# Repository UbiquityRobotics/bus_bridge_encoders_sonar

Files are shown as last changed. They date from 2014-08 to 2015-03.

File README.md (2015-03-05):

# bus_bridge_encoders_sonar

The are currently 4 revisions -- `rev_a`, `rev_b`, `rev_c`,
and `rev_d`.  The schematic is available as bus_bridge_encoders_sonar.pdf`
or as `bus_bridge_encoders_sonar.svg` in the appropriate revision
directory.

## Rev. A Issues

* Tie off unused inputs of U7 to 0V or 5V. [x]

* Replace R8, R9, R10, R11, R12, R13 with a 10K ohm SIP package. [x]

* Add protection diodes to the motor outputs.  The 754410 does
  **not** have protection diodes like the L793D did.  [No.  If
  it is an issue, use the L293D instead.]

* Adding a 2x3 pin ISP programming header. [x]

* The U8 TXD (pin 1) and RXD (pin 4) are swapped. [x]

* Replace the R17, R18, R20, R21 voltage dividers with 100K pull-ups. [x]

* Add a 100K pull up U7A pin 1 to protect against U8 not
  being plugged in. [x]

* Combine Encoder and Motor onto a single 2x4 ribbon cable. [x]

* Add an LED that can be blinked. [x]

## Rev. B Issues

* Connected U8 STBY (pin 8) to a processor pin [x]

## Rev. C Docummentation

<Table Border="1">
    <TR>
    </TR><TR>
	<TH>Arduino Name</TH>
	<TH>AVR Port</TH>
	<TH>Function</TH>
    </TR><TR>
	<TD>D0</TD>
	<TD>PD0/RXD</TD>
	<TD>USART Receive</TD>
    </TR><TR>
	<TD>D1</TD>
	<TD>PD0/TXD</TD>
	<TD>USART Transmit</TD.
    </TR><TR>
	<TD>D2</TD>
	<TD>PD3</TD>
	<TD>SONAR0_TRIG</TD>
    </TR><TR>
	<TD>D3</TD>
	<TD>PD3/OC2B</TD>
	<TD>SONAR0_ECHO</TD>
    </TR><TR>
	<TD>D4</TD>
	<TD>PD4</TD>
	<TD>SONAR1_TRIG</TD>
    </TR><TR>
	<TD>D5</TD>
	<TD>PD6/OC0B</TD>
	<TD>SONAR1_ECHO</TD>
    </TR><TR>
	<TD>D6</TD>
	<TD>PD6/OC0A</TD>
	<TD>ENC_EN</TD>
    </TR><TR>cc
	<TD>D7</TD>
        <TD>PD7<TD>
	<TD>1A</TD>
    </TR><TR>
	<TD>D8</TD>
	<TD>PB0<TD>
	<TD>4A</TD>
    </TR><TR>
	<TD>D9</TD>
	<TD>PB1/OC1A</TD>
	<TD>EN34</TD>
    </TR><TR>
	<TD>D10</TD>
	<TD>PB2/OC1B</TD>
	<TD>EN12</TD>
    </TR><TR>
	<TD>D11</TD>
	<TD>PB3/OC2A</TD>
	<TD>3A</TD>
    </TR><TR>
	<TD>D12</TD>m
	<TD>PB4</TD>
	<TD>2A</TD>
    </TR><TR>
	<TD>D13</TD>
	<TD>PB5</TD>
	<TD>LED</TD>
    </TR><TR>
	<TD>A0</TD>
	<TD>PC0</TD>
	<TD>ENC1_A</TD>
    </TR><TR>
	<TD>A1</TD>
	<TD>PC1</TD>
	<TD>ENC1_B</TD>
    </TR><TR>
	<TD>A2</TD>
	<TD>PC2</TD>
	<TD>ENC2_A</TD>
    </TR><TR>
	<TD>A3</TD>
	<TD>PC3</TD>
	<TD>ENC2_B</TD>
    </TR><TR>
	<TD>A4</TD>
	<TD>PC4</TD>
	<TD>CAN_STBY</TD>
    </TR><TR>
	<TD>A5</TD>
	<TD>PC5</TD>
	<TD>-</TD>
    </TR>
</Table>

## Rev. C Issues

* Schematic should label C13 as 1uF. [x]

* Schematic should label R4 as 120_1%. [x]

* Schematic has BGND and BPWR swapped on root diagram. [x]

* Make sure regulator input capacitors can take 30V.  Probably switch
  over to aluminum electrolytic capacitor. [x]

* Move ISP connector up to make more room for Atmel-ICE connector. [x]

* Between Dual Slot Encoder (Rev. D) and Rev. C of this
  board, pins 4 and 5 are swapped as are pins 6 and 7.
  [change dual slot encoders instead]
  See below:

<BlockQuote>
<Pre>
     BBES-C       DSE-D
    ===========================
     MOTOR_A   1  MOTOR_A
     MOTOR_A   2  MOTOR_A
     LOG_5V    3  LPWR (=5V)
     LGND      4  QUAD_A
     QUAD_A    5  LGND (not really used)
     QUAD_B    6  LED_EN
     LED_EN    7  QUAD_B
     LED_5V    8  BPWR
     MOTOR_B   9  MOTOR_B
     MOTOR_B  10  MOTOR_B
</Pre>
</BlockQuote>

## Rev. D Issues

* The vertical resistors are hard to solder.  Think about switching

* Update schematic to specifiy electrolytic capacistors for input
  voltage regulators.

* The C5 is too close to the mounting hole.

* Think about adding an LED jumper block.

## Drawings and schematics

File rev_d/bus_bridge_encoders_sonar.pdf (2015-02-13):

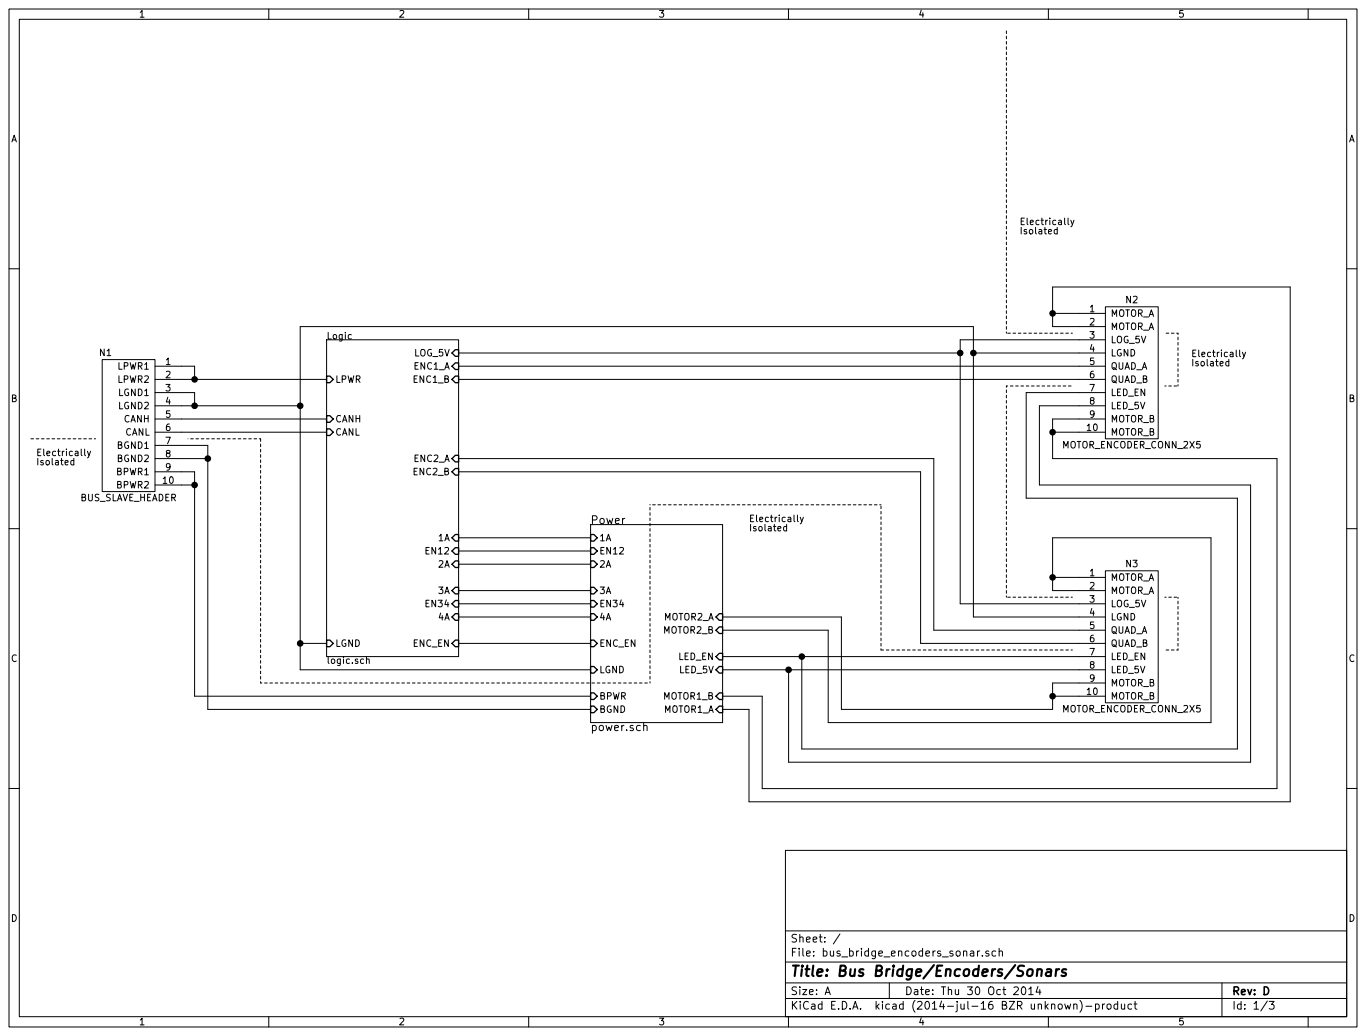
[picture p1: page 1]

File: bus_bridge_encoders_sonar.sch Sheet: /
Id: 1/3 Title: Bus Bridge/Encoders/Sonars

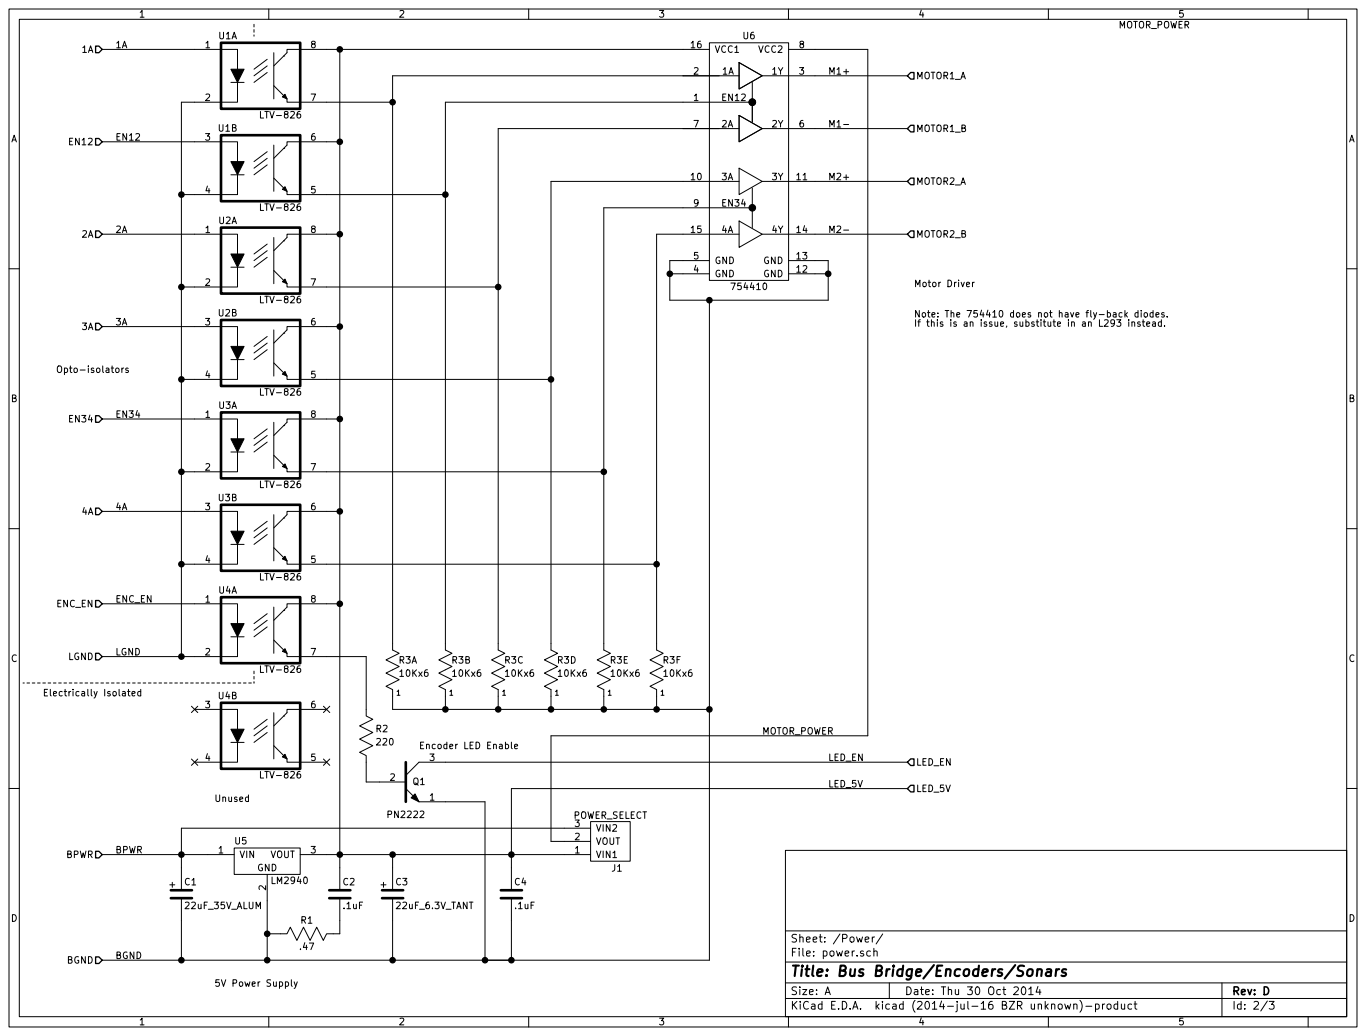
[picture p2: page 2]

If this is an issue, substitute in an L293 instead. LED_5V MOTOR_POWER

File: power.sch Sheet: /Power/ BPWR

Id: 2/3 Title: Bus Bridge/Encoders/Sonars

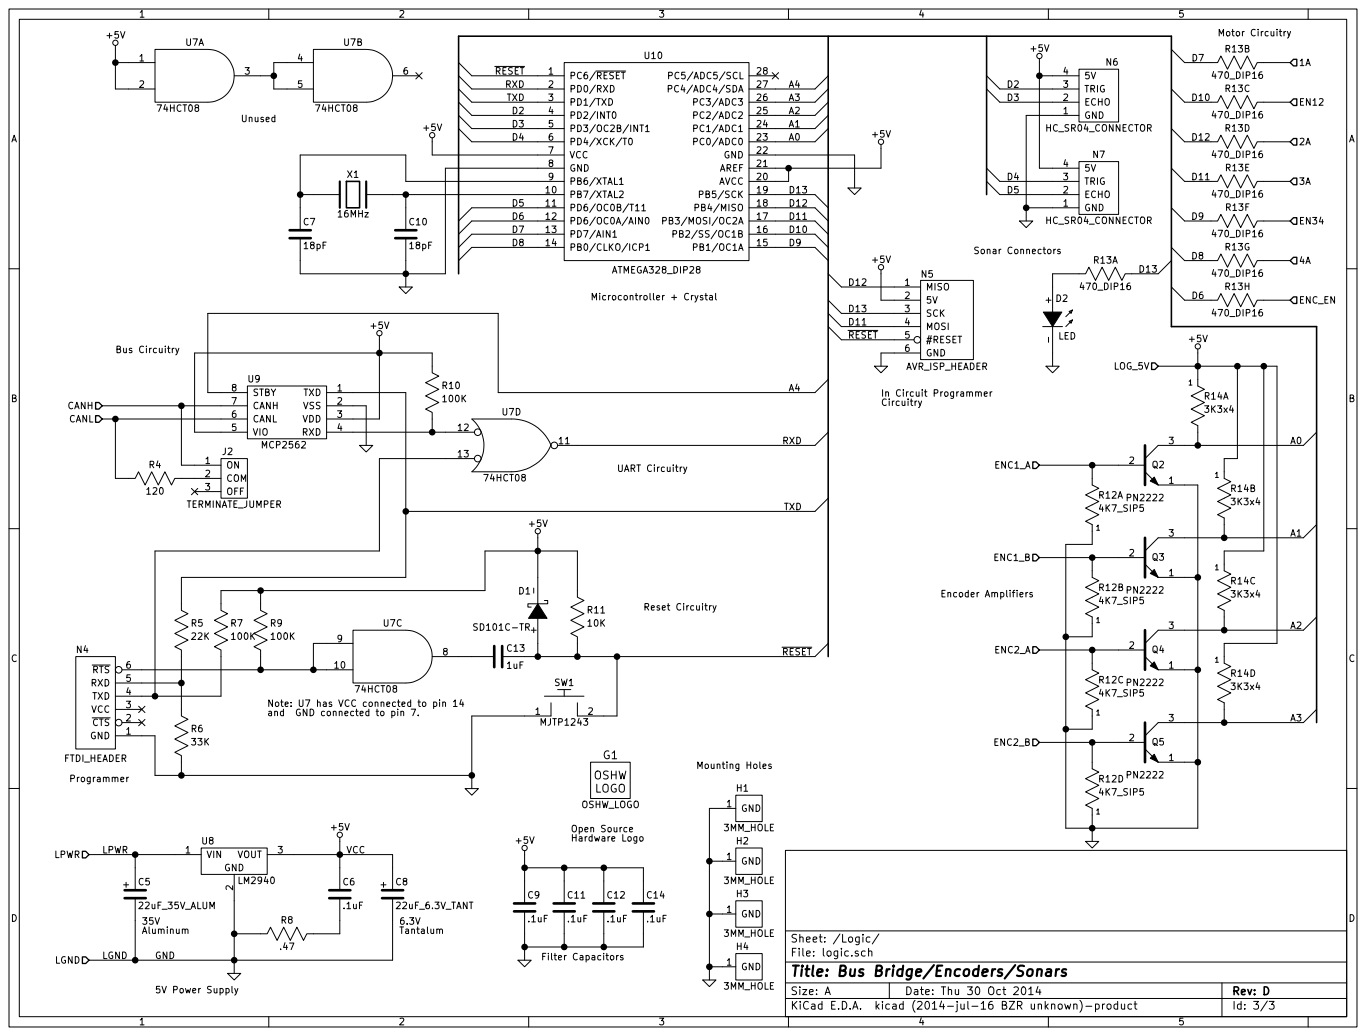
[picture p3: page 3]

UnusedNote: U7 has VCC connected to pin 14

and GND connected to pin 7.

File: logic.sch
Id: 3/3 Title: Bus Bridge/Encoders/Sonars

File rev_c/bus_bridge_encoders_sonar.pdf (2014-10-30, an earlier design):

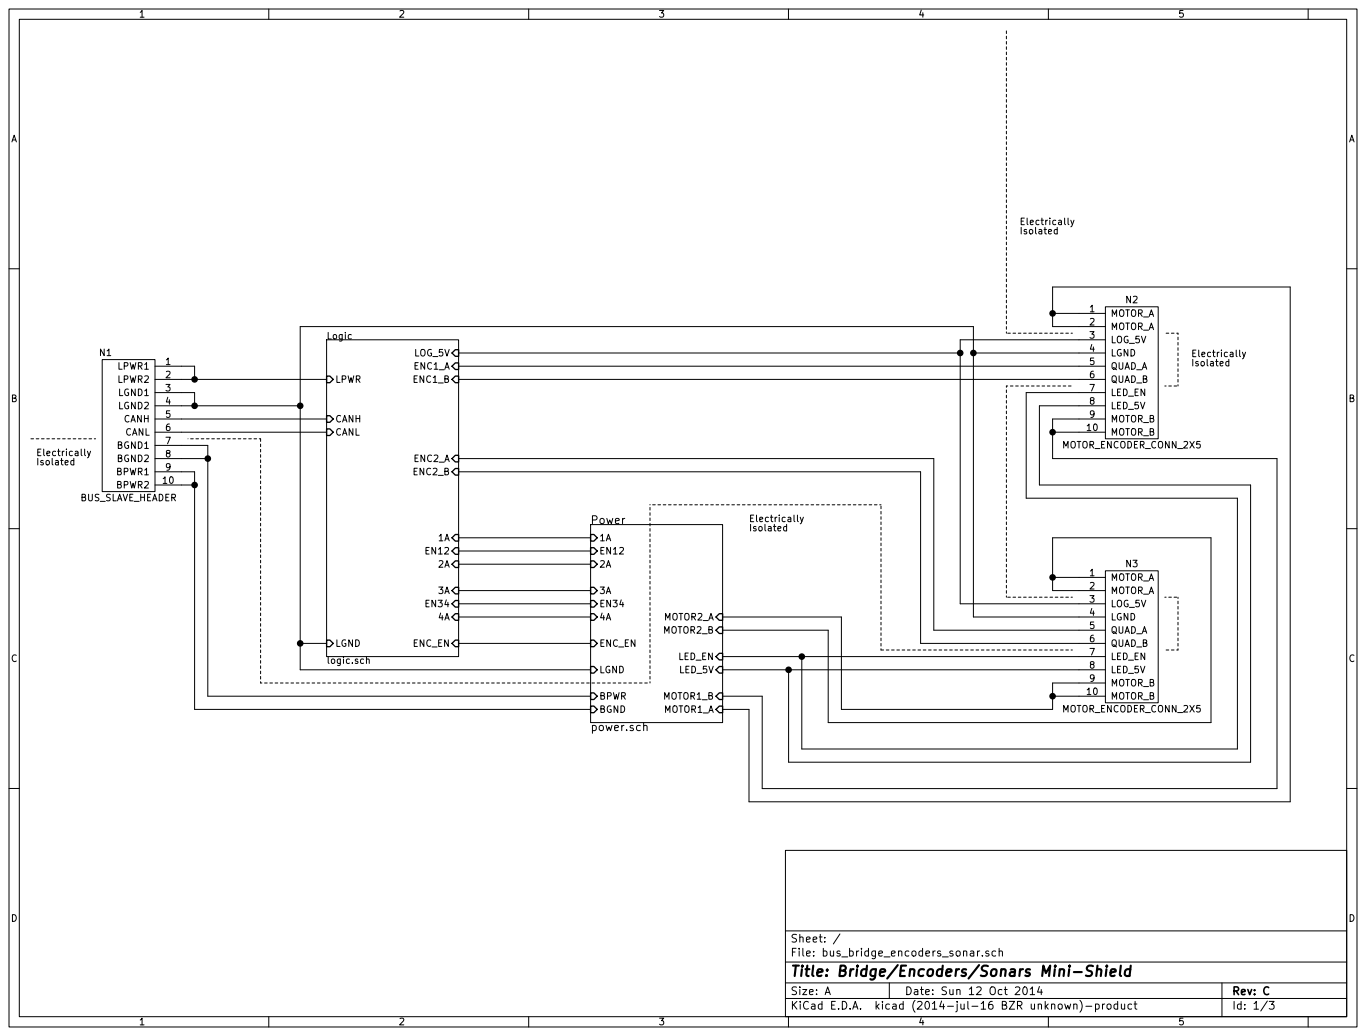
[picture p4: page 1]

File: bus_bridge_encoders_sonar.sch Sheet: /
Id: 1/3 Title: Bridge/Encoders/Sonars Mini-Shield

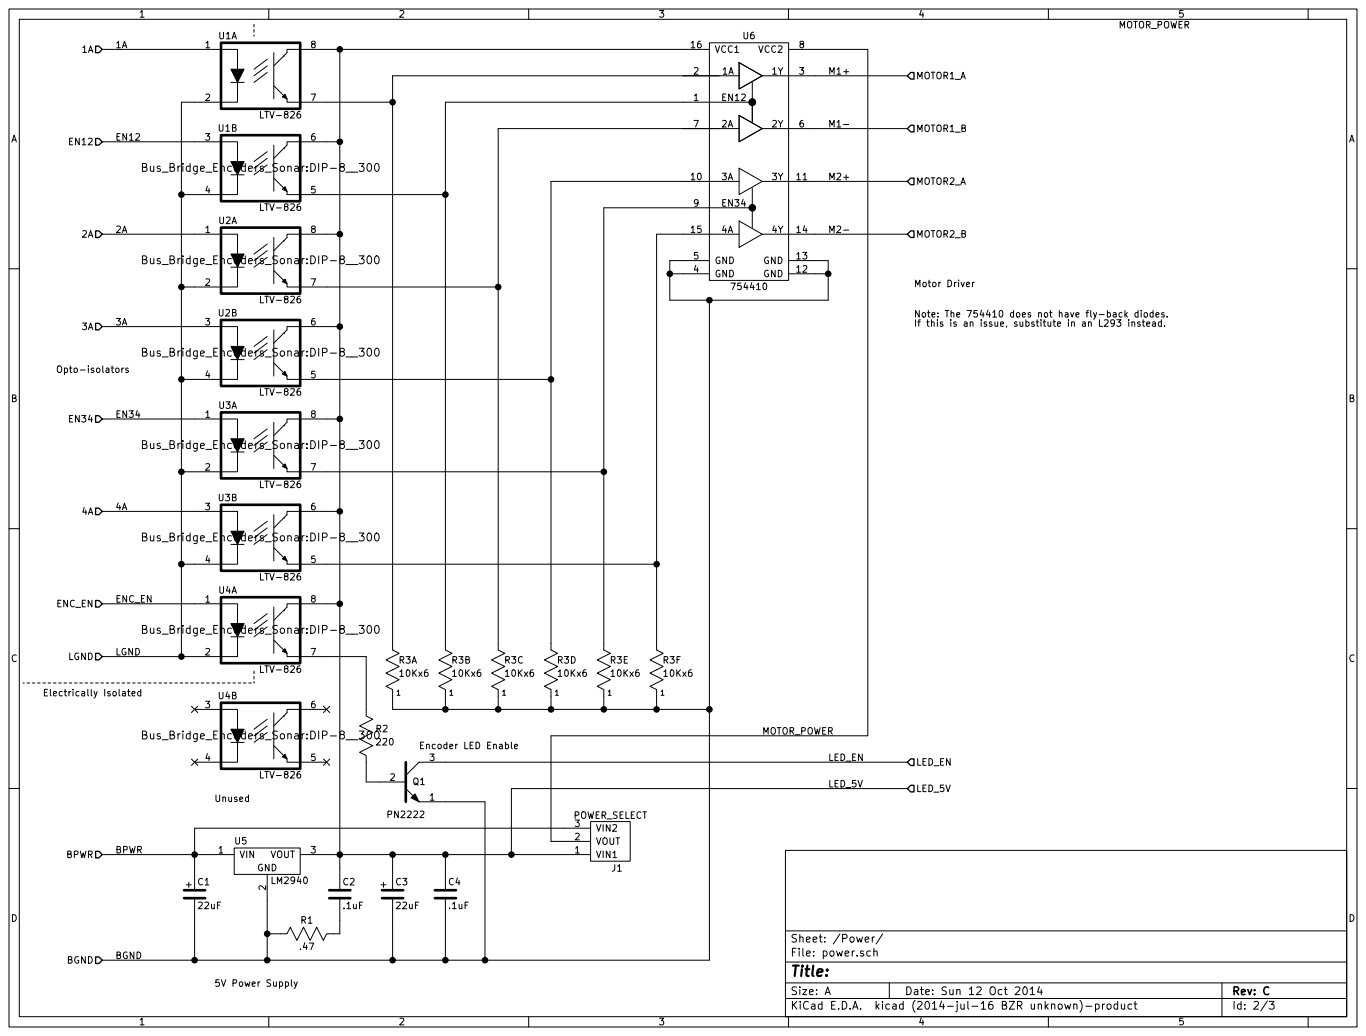
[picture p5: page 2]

If this is an issue, substitute in an L293 instead. LED_5V MOTOR_POWER

File: power.sch Sheet: /Power/ BPWR

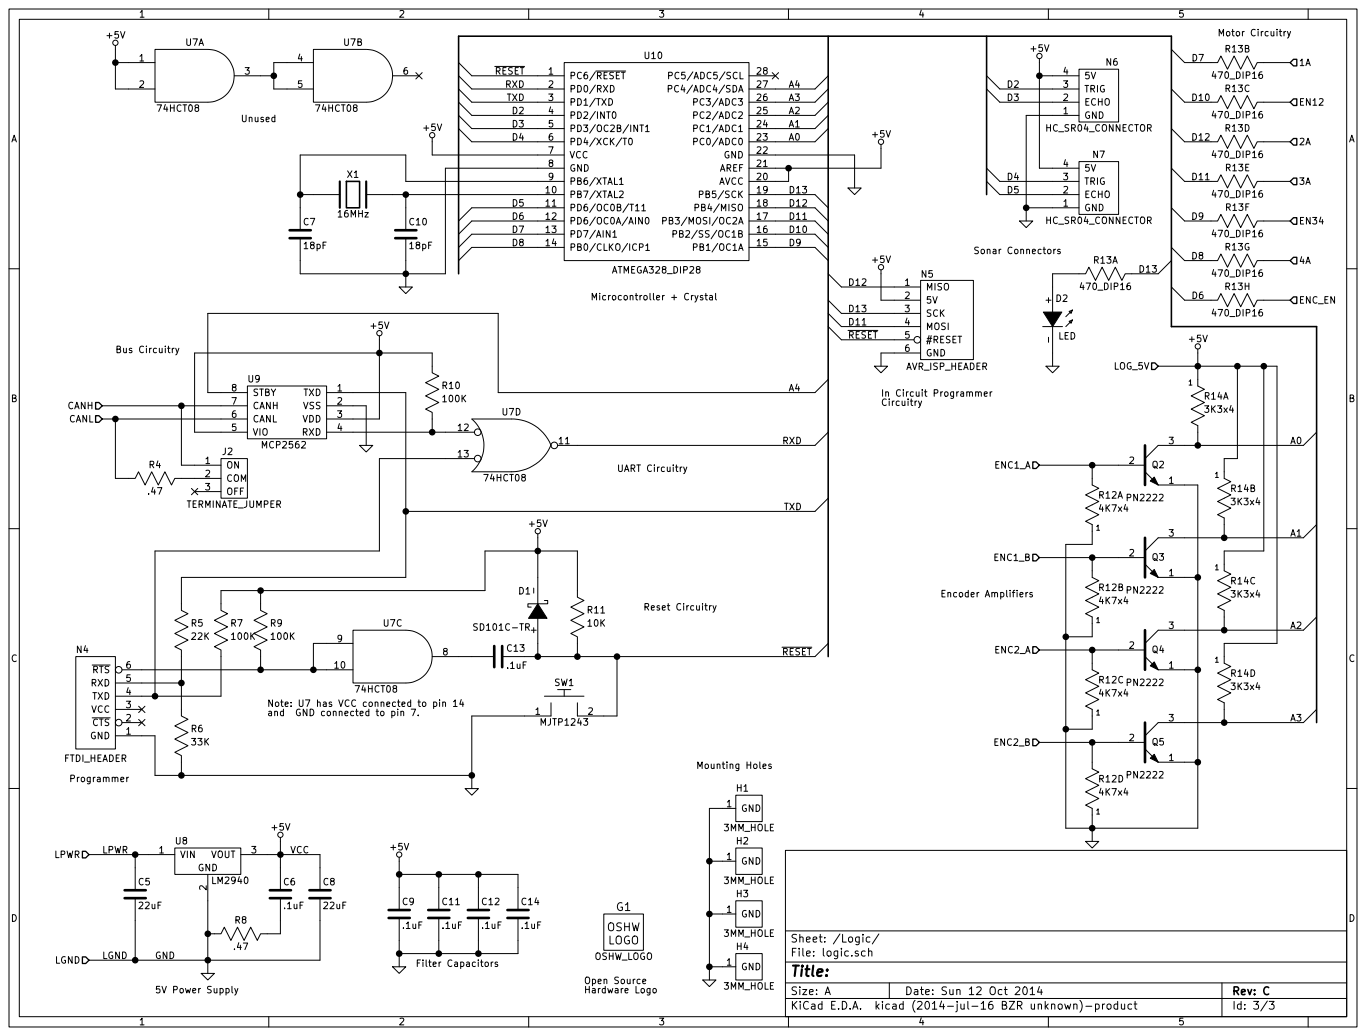
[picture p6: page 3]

UnusedNote: U7 has VCC connected to pin 14

and GND connected to pin 7.

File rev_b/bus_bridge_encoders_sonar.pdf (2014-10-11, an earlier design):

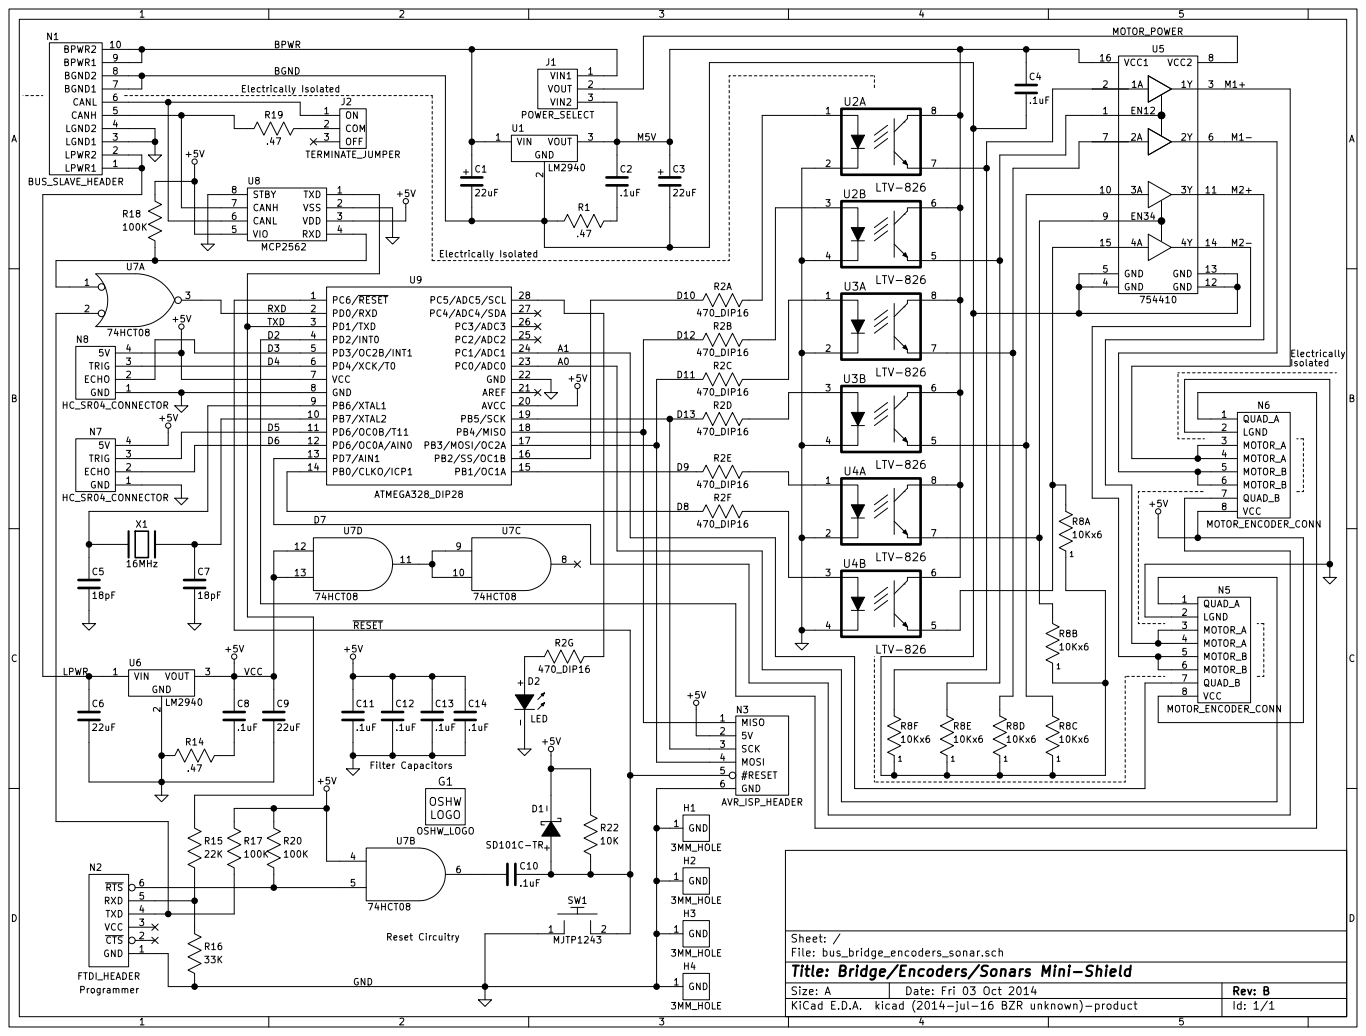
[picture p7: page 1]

File: bus_bridge_encoders_sonar.sch Sheet: / GND 1 H1

Id: 1/1 Title: Bridge/Encoders/Sonars Mini-Shield

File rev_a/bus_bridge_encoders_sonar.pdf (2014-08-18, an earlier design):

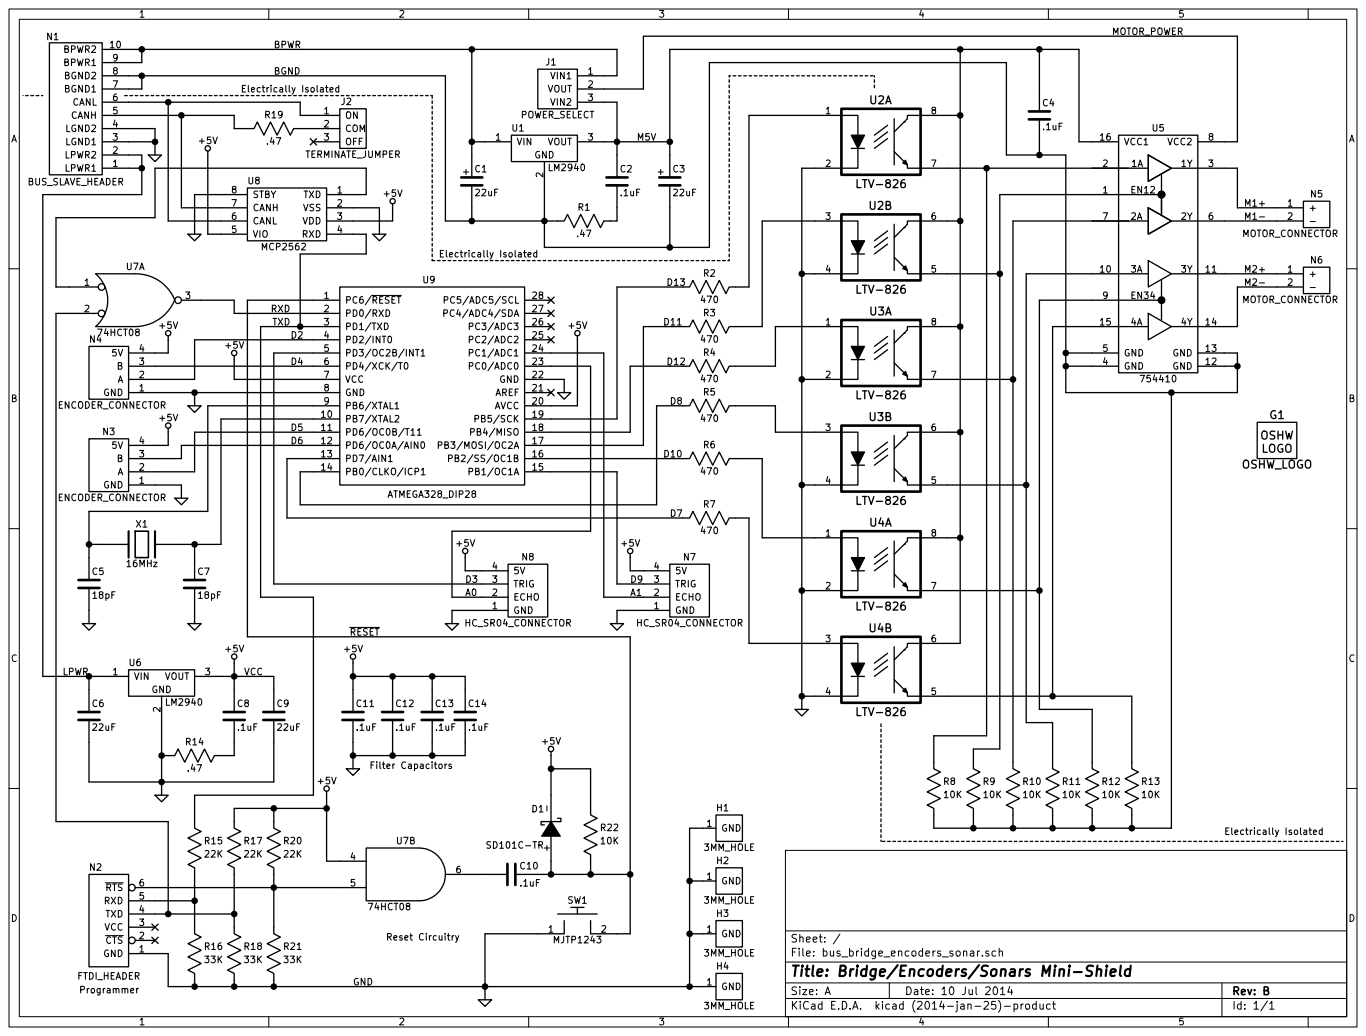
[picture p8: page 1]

File: bus_bridge_encoders_sonar.sch Sheet: / GND 1 H1

Id: 1/1 Title: Bridge/Encoders/Sonars Mini-Shield

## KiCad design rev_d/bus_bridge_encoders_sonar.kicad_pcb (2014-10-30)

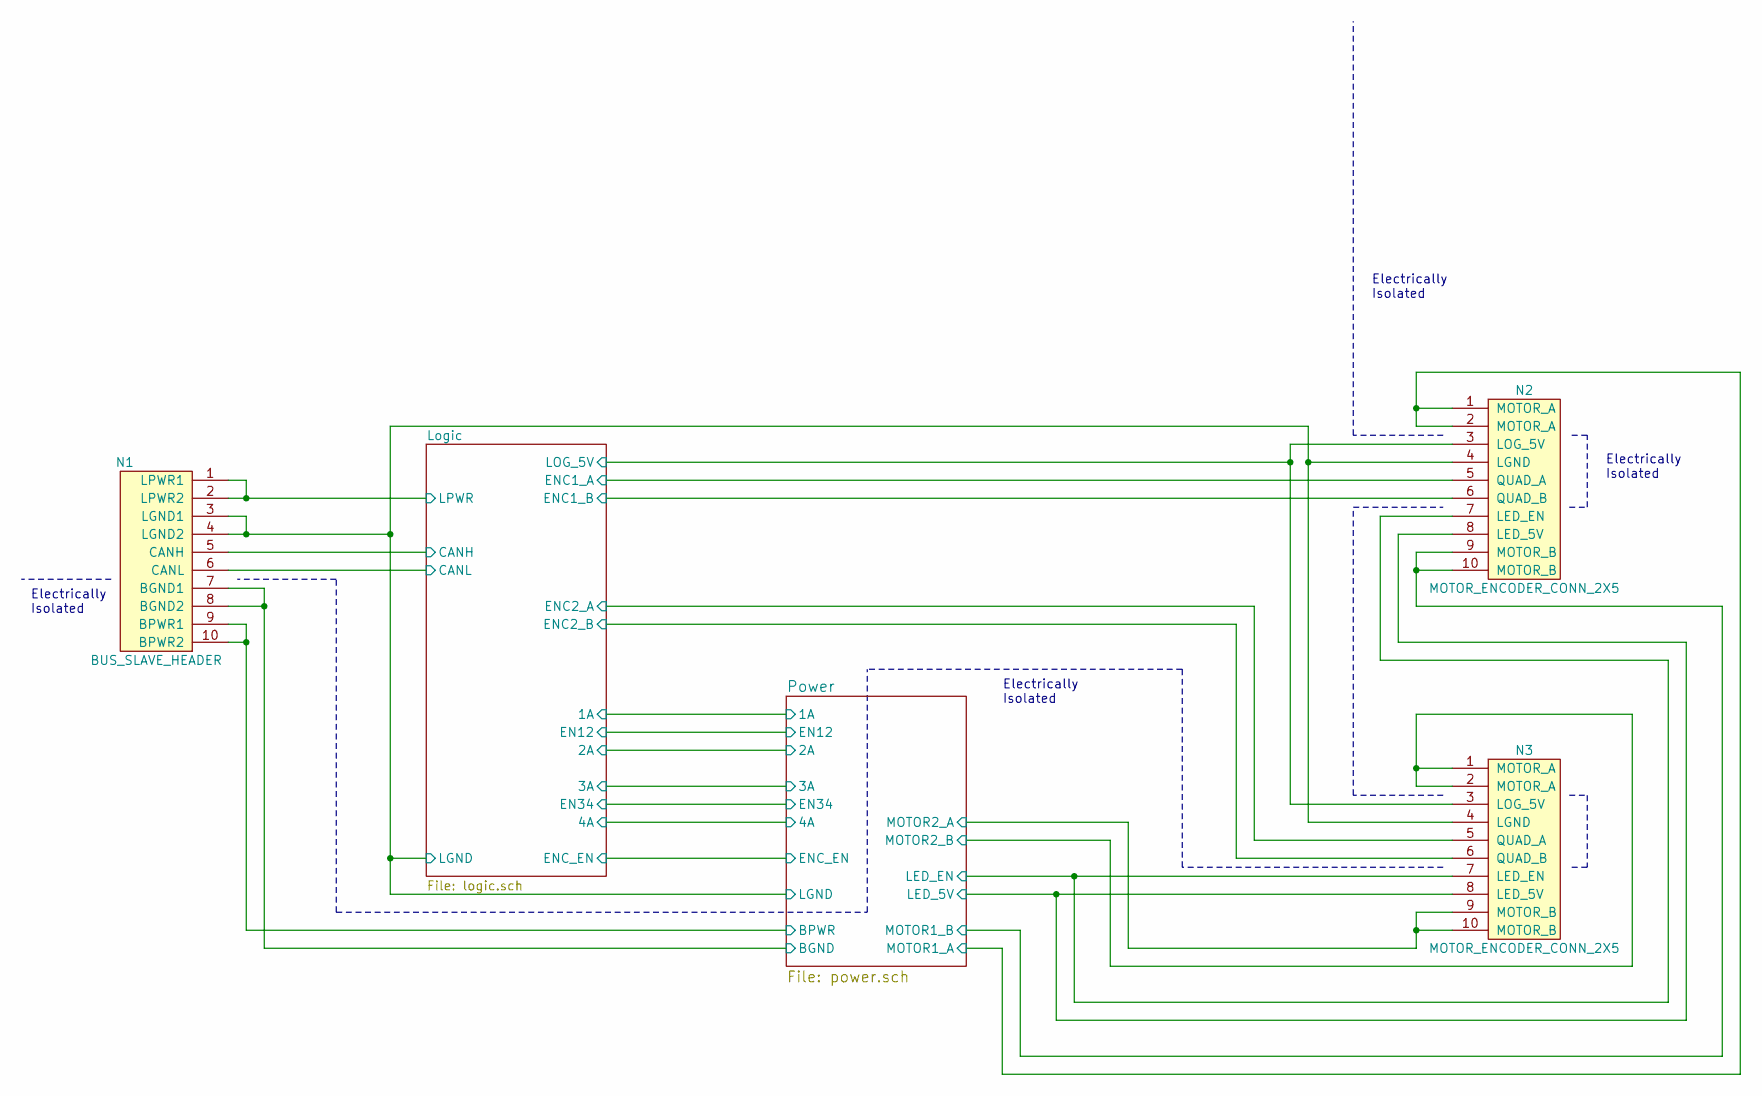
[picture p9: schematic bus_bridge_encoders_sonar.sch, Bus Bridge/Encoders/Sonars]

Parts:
N1: BUS_SLAVE_HEADER; Pin_Header_Straight_2x05_Shrouded
N2, N3: MOTOR_ENCODER_CONN_2X5; Pin_Header_Straight_2x05_Shrouded

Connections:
+5V: N2.3 (LOG_5V), N3.3 (LOG_5V); also elsewhere on the board
/Logic/CANH: N1.5 (CANH); also elsewhere on the board
/Logic/CANL: N1.6 (CANL); also elsewhere on the board
/Logic/ENC1_A: N2.5 (QUAD_A); also elsewhere on the board
/Logic/ENC1_B: N2.6 (QUAD_B); also elsewhere on the board
/Logic/ENC2_A: N3.5 (QUAD_A); also elsewhere on the board
/Logic/ENC2_B: N3.6 (QUAD_B); also elsewhere on the board
/Logic/LPWR: N1.1 (LPWR1), N1.2 (LPWR2); also elsewhere on the board
/Power/BGND: N1.7 (BGND1), N1.8 (BGND2); also elsewhere on the board
/Power/BPWR: N1.9 (BPWR1), N1.10 (BPWR2); also elsewhere on the board
/Power/LED_5V: N2.8 (LED_5V), N3.8 (LED_5V); also elsewhere on the board
/Power/LED_EN: N2.7 (LED_EN), N3.7 (LED_EN); also elsewhere on the board
/Power/MOTOR1_A: N2.1 (MOTOR_A), N2.2 (MOTOR_A); also elsewhere on the board
/Power/MOTOR1_B: N2.9 (MOTOR_B), N2.10 (MOTOR_B); also elsewhere on the board
/Power/MOTOR2_A: N3.9 (MOTOR_B), N3.10 (MOTOR_B); also elsewhere on the board
/Power/MOTOR2_B: N3.1 (MOTOR_A), N3.2 (MOTOR_A); also elsewhere on the board
GND: N1.3 (LGND1), N1.4 (LGND2), N2.4 (LGND), N3.4 (LGND); also elsewhere on the board

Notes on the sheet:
Electrically Isolated

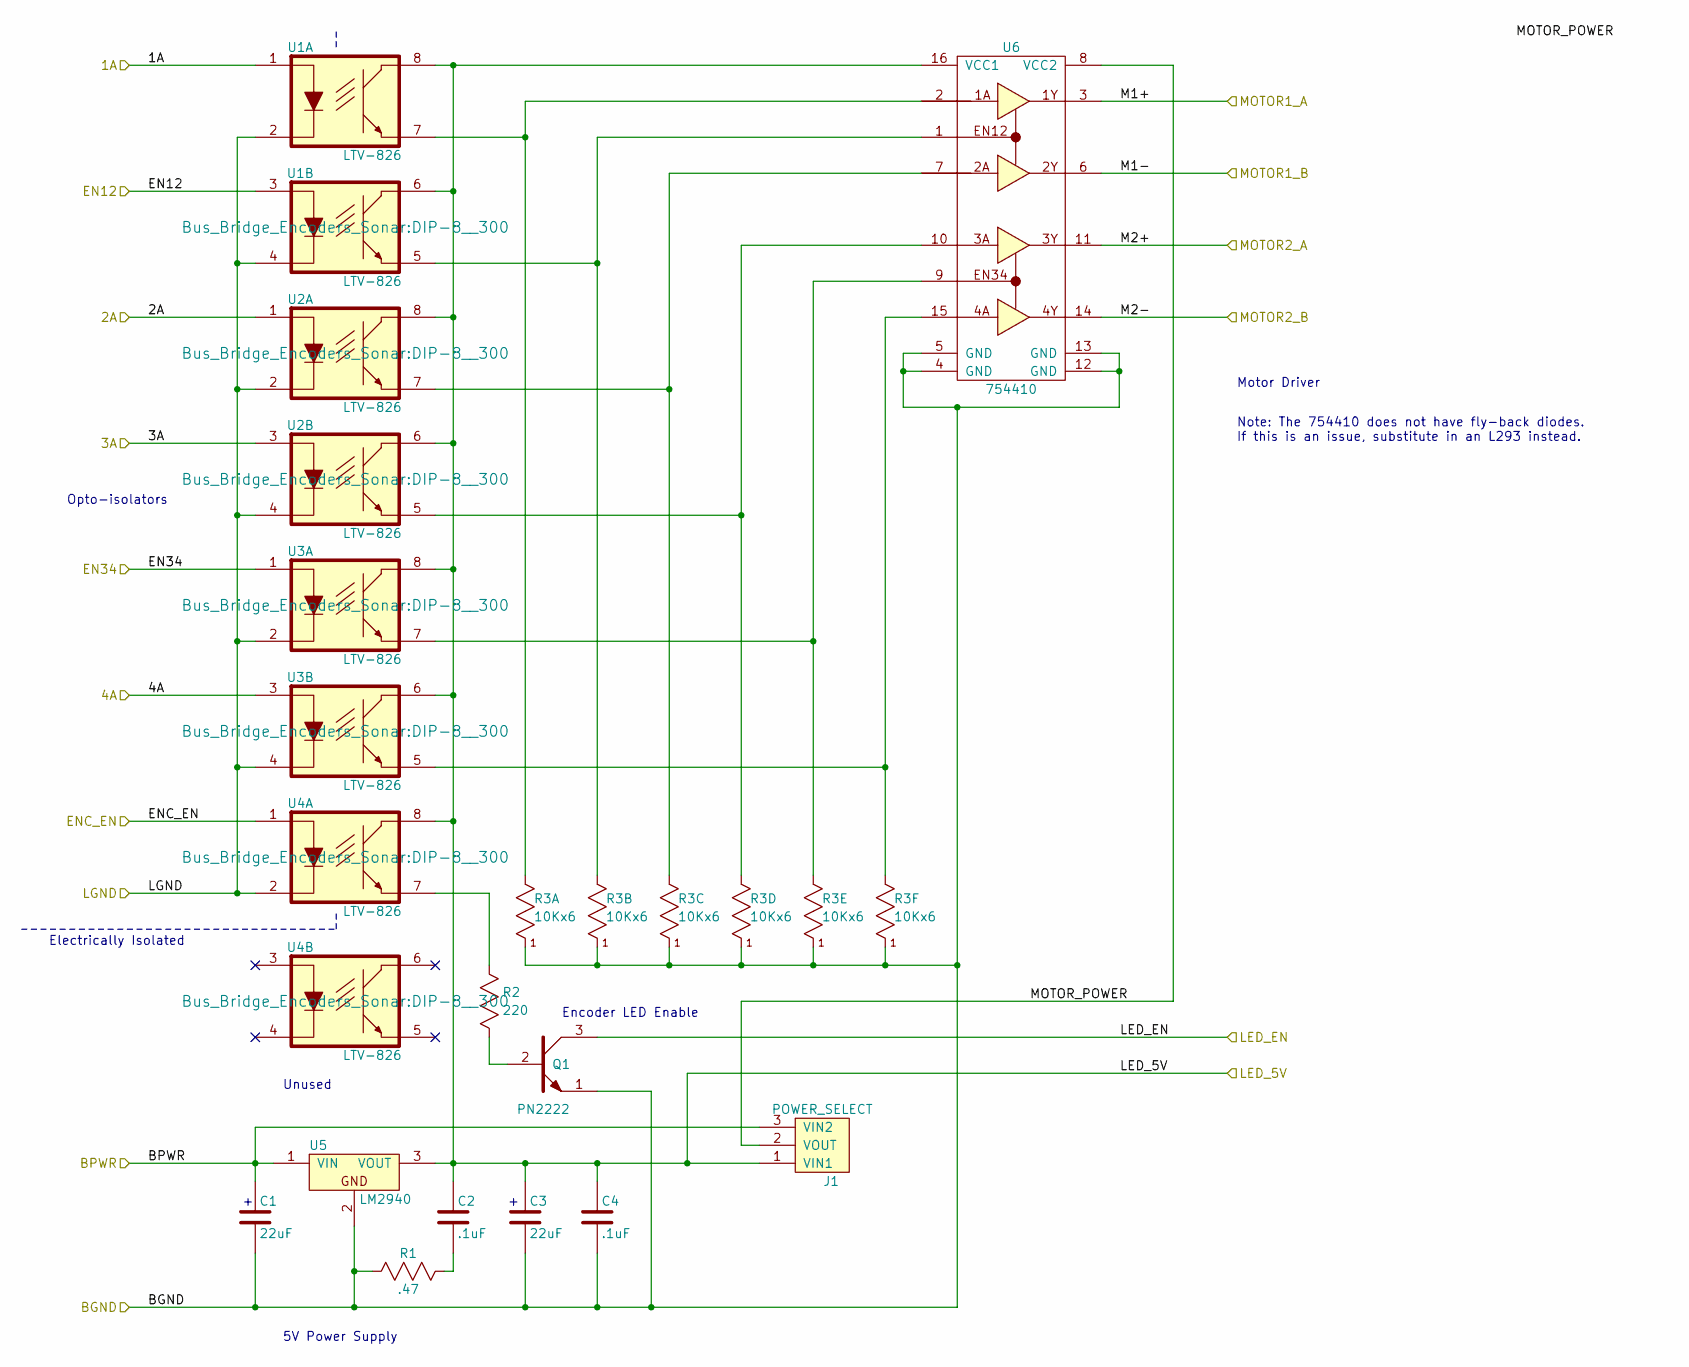
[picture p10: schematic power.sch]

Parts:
C1, C3: 22uF; Capacitor3MMDiscRM2.5
C2, C4: .1uF; Capacitor4x3RM2-5_RevB
J1: POWER_SELECT; Pin_Header_Straight_1x03
Q1: PN2222; TO92_123
R1: .47; Pin_Header_Straight_1x02
R2: 220; Pin_Header_Straight_1x02
R3: 10Kx6; Pin_Header_Straight_1x07
U1, U2, U3, U4: LTV-826; DIP-8__300
U5: LM2940; TO-220_Neutral123_Horizontal_LargePads
U6: 754410; DIP-16__300

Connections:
/Logic/1A: U1.1; also elsewhere on the board
/Logic/2A: U2.1; also elsewhere on the board
/Logic/3A: U2.3; also elsewhere on the board
/Logic/4A: U3.3; also elsewhere on the board
/Logic/EN12: U1.3; also elsewhere on the board
/Logic/EN34: U3.1; also elsewhere on the board
/Logic/ENC_EN: U4.1; also elsewhere on the board
/Power/BGND: C1.2, C3.2, C4.2, Q1.1, R1.1, R3.1, U5.2, U6.4 (GND), U6.5 (GND), U6.12 (GND), U6.13 (GND); also elsewhere on the board
/Power/BPWR: C1.1, J1.3 (VIN2), U5.1 (VIN); also elsewhere on the board
/Power/LED_5V: C2.1, C3.1, C4.1, J1.1 (VIN1), U1.6, U1.8, U2.6, U2.8, U3.6, U3.8, U4.8, U5.3 (VOUT), U6.16 (VCC1); also elsewhere on the board
/Power/LED_EN: Q1.3; also elsewhere on the board
/Power/MOTOR1_A: U6.3 (1Y); also elsewhere on the board
/Power/MOTOR1_B: U6.6 (2Y); also elsewhere on the board
/Power/MOTOR2_A: U6.11 (3Y); also elsewhere on the board
/Power/MOTOR2_B: U6.14 (4Y); also elsewhere on the board
/Power/MOTOR_POWER: J1.2 (VOUT), U6.8 (VCC2)
GND: U1.2, U1.4, U2.2, U2.4, U3.2, U3.4, U4.2; also elsewhere on the board
unnamed: C2.2, R1.2
unnamed: Q1.2, R2.1
unnamed: R2.2, U4.7
unnamed: R3.2, U1.7, U6.2 (1A)
unnamed: R3.3, U1.5, U6.1 (EN12)
unnamed: R3.4, U2.7, U6.7 (2A)
unnamed: R3.5, U2.5, U6.10 (3A)
unnamed: R3.6, U3.7, U6.9 (EN34)
unnamed: R3.7, U3.5, U6.15 (4A)

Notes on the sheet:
Electrically Isolated
Unused
5V Power Supply
Encoder LED Enable
Opto-isolators
Motor Driver
Note: The 754410 does not have fly-back diodes. If this is an issue, substitute in an L293 instead.

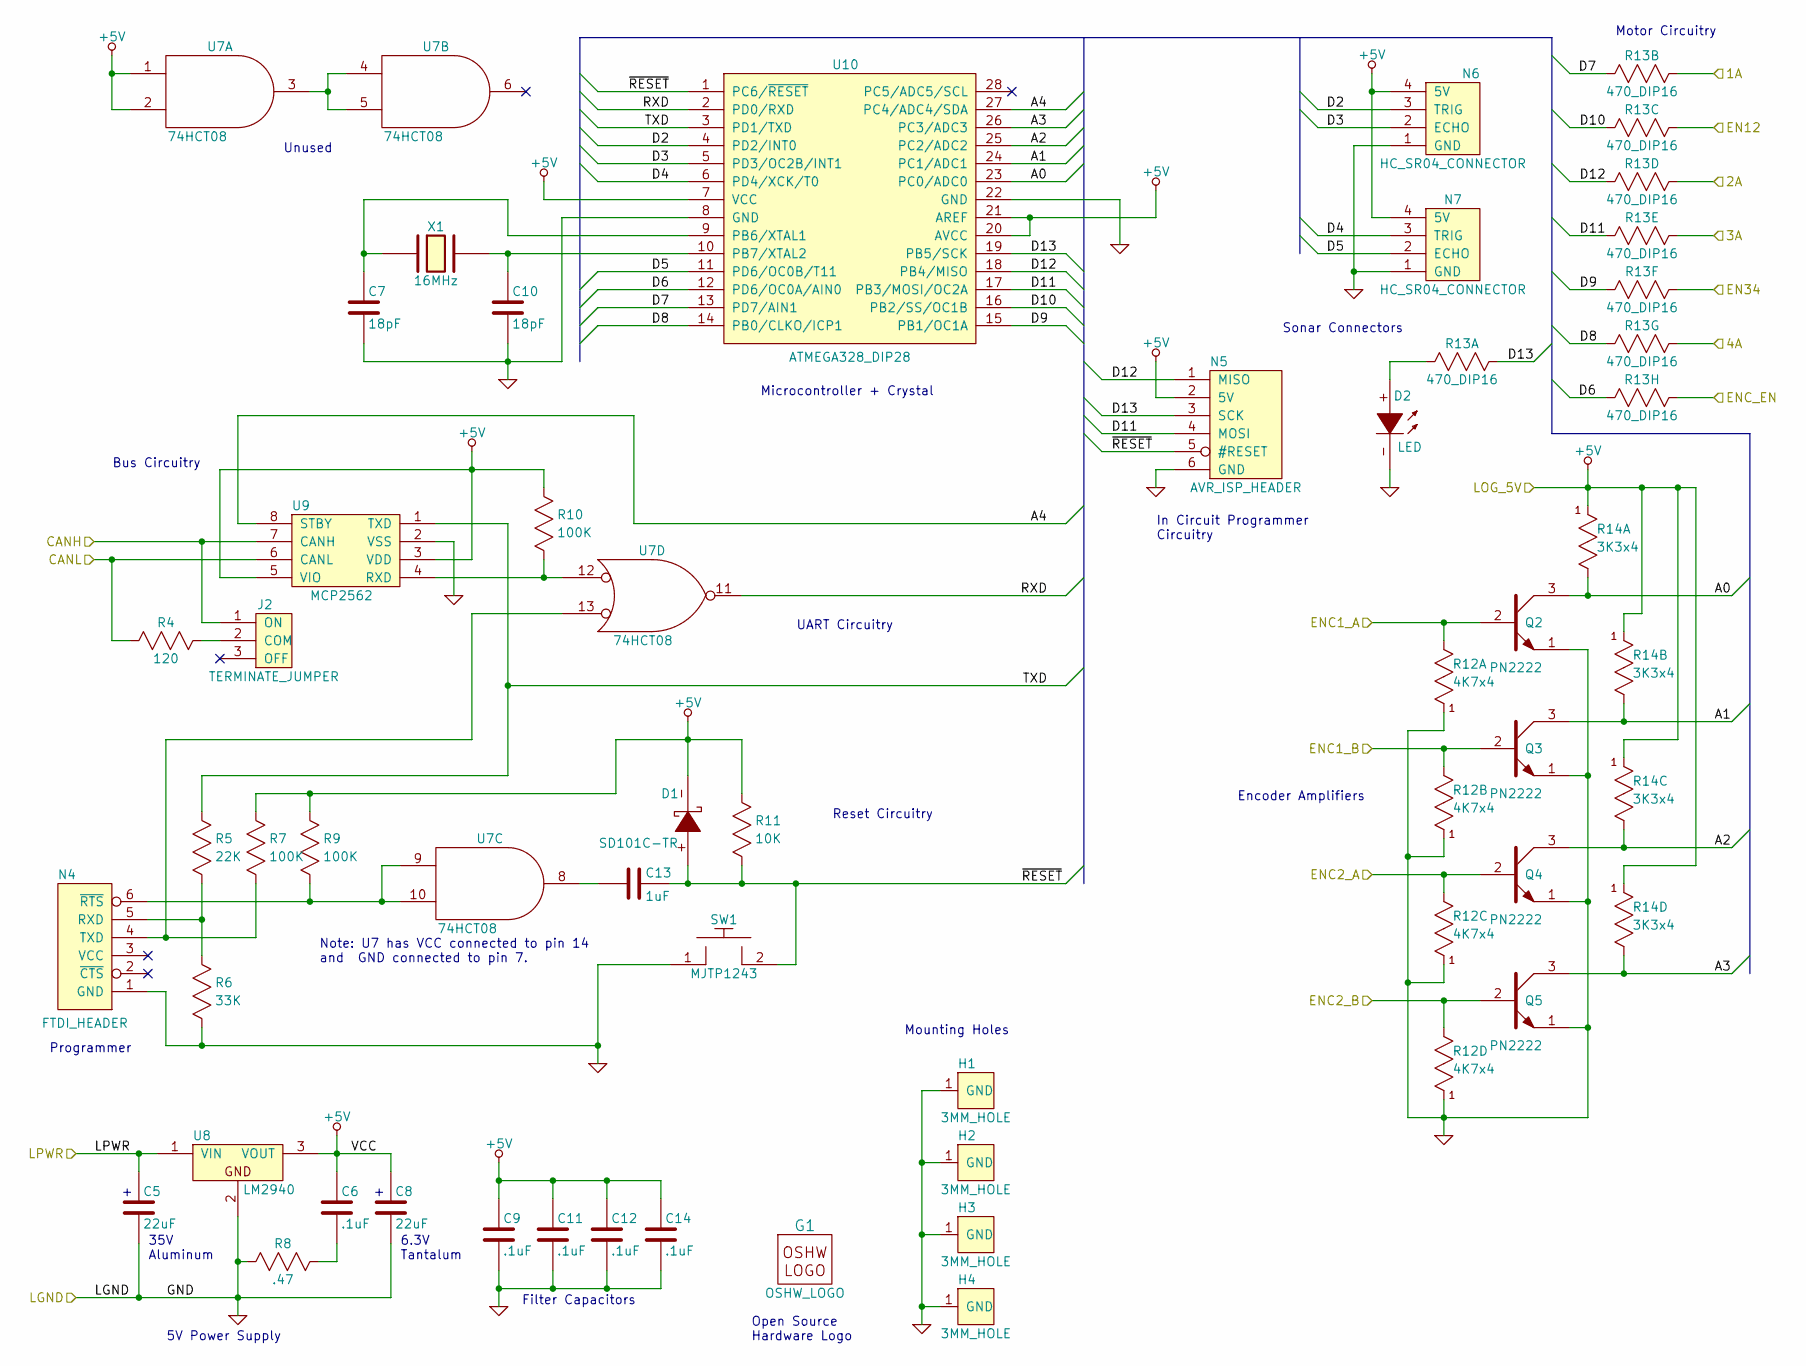
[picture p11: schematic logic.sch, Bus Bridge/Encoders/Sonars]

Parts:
C5, C8: 22uF; Capacitor3MMDiscRM2.5
C6, C9, C11, C12, C14: .1uF; Capacitor4x3RM2-5_RevB
C7, C10: 18pF; Capacitor4x3RM2-5_RevB
C13: 1uF; Capacitor4x3RM2-5_RevB
D1: SD101C-TR; Diode_DO-41_SOD81_Horizontal_RM10
D2: LED; T1_LED
G1: OSHW_LOGO; OSHW_LOGO_300mil
H1, H2, H3, H4: 3MM_HOLE; MountingHole_3mm
J2: TERMINATE_JUMPER; Pin_Header_Straight_1x03
N4: FTDI_HEADER; Pin_Header_Straight_1x06
N5: AVR_ISP_HEADER; Pin_Header_Straight_2x03
N6, N7: HC_SR04_CONNECTOR; Pin_Header_Straight_1x04
Q2, Q3, Q4, Q5: PN2222; TO92_123
R4: 120; Pin_Header_Straight_1x02
R5: 22K; Pin_Header_Straight_1x02
R6: 33K; Pin_Header_Straight_1x02
R7, R9, R10: 100K; Pin_Header_Straight_1x02
R8: .47; Pin_Header_Straight_1x02
R11: 10K; Pin_Header_Straight_1x02
R12: 4K7x4; Pin_Header_Straight_1x05
R13: 470_DIP16; DIP-16__300
R14: 3K3x4; Pin_Header_Straight_1x05
SW1: MJTP1243; Button_6.5MM
U7: 74HCT08; DIP-14__300
U8: LM2940; TO-220_Neutral123_Horizontal_LargePads
U9: MCP2562; DIP-8__300
U10: ATMEGA328_DIP28; DIP-28__300
X1: 16MHz; Crystal_HC49-U_Vertical

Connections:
+5V: C6.1, C8.1, C9.1, C11.1, C12.1, C14.1, D1.-, N5.2 (5V), N6.4 (5V), N7.4 (5V), R7.2, R9.2, R10.2, R11.2, R14.1, U7.1, U7.2, U7.14 (VCC), U8.3 (VOUT), U9.3 (VDD), U9.5 (VIO), U10.7 (VCC), U10.20 (AVCC), U10.21 (AREF); also elsewhere on the board
/Logic/1A: R13.15 (B); also elsewhere on the board
/Logic/2A: R13.13 (B); also elsewhere on the board
/Logic/3A: R13.12 (B); also elsewhere on the board
/Logic/4A: R13.10 (B); also elsewhere on the board
/Logic/A0: Q2.3, R14.2, U10.23 (PC0/ADC0)
/Logic/A1: Q3.3, R14.3, U10.24 (PC1/ADC1)
/Logic/A2: Q4.3, R14.4, U10.25 (PC2/ADC2)
/Logic/A3: Q5.3, R14.5, U10.26 (PC3/ADC3)
/Logic/A4: U9.8 (STBY), U10.27 (PC4/ADC4/SDA)
/Logic/CANH: J2.1 (ON), U9.7 (CANH); also elsewhere on the board
/Logic/CANL: R4.1, U9.6 (CANL); also elsewhere on the board
/Logic/D2: N6.3 (TRIG), U10.4 (PD2/INT0)
/Logic/D3: N6.2 (ECHO), U10.5 (PD3/OC2B/INT1)
/Logic/D4: N7.3 (TRIG), U10.6 (PD4/XCK/T0)
/Logic/D5: N7.2 (ECHO), U10.11 (PD6/OC0B/T11)
/Logic/D6: R13.8 (A), U10.12 (PD6/OC0A/AIN0)
/Logic/D7: R13.2 (A), U10.13 (PD7/AIN1)
/Logic/D8: R13.7 (A), U10.14 (PB0/CLKO/ICP1)
/Logic/D9: R13.6 (A), U10.15 (PB1/OC1A)
/Logic/D10: R13.3 (A), U10.16 (PB2/SS/OC1B)
/Logic/D11: N5.4 (MOSI), R13.5 (A), U10.17 (PB3/MOSI/OC2A)
/Logic/D12: N5.1 (MISO), R13.4 (A), U10.18 (PB4/MISO)
/Logic/D13: N5.3 (SCK), R13.16 (B), U10.19 (PB5/SCK)
/Logic/EN12: R13.14 (B); also elsewhere on the board
/Logic/EN34: R13.11 (B); also elsewhere on the board
/Logic/ENC1_A: Q2.2, R12.2; also elsewhere on the board
/Logic/ENC1_B: Q3.2, R12.3; also elsewhere on the board
/Logic/ENC2_A: Q4.2, R12.4; also elsewhere on the board
/Logic/ENC2_B: Q5.2, R12.5; also elsewhere on the board
/Logic/ENC_EN: R13.9 (B); also elsewhere on the board
/Logic/LPWR: C5.1, U8.1 (VIN); also elsewhere on the board
/Logic/RXD: U7.11, U10.2 (PD0/RXD)
/Logic/TXD: R5.2, U9.1 (TXD), U10.3 (PD1/TXD)
/Logic/~RESET: C13.2, D1.+, N5.5 (#RESET), R11.1, SW1.2, U10.1 (PC6/~RESET)
GND: C5.2, C7.2, C8.2, C9.2, C10.2, C11.2, C12.2, C14.2, D2.-, H1.1, H2.1, H3.1, H4.1, N4.1 (GND), N5.6 (GND), N6.1 (GND), N7.1 (GND), Q2.1, Q3.1, Q4.1, Q5.1, R6.1, R8.1, R12.1, SW1.1, U7.7 (GND), U8.2, U9.2 (VSS), U10.8 (GND), U10.22 (GND); also elsewhere on the board
unnamed: C6.2, R8.2
unnamed: C7.1, U10.9 (PB6/XTAL1), X1.1
unnamed: C10.1, U10.10 (PB7/XTAL2), X1.2
unnamed: C13.1, U7.8
unnamed: D2.+, R13.1 (A)
unnamed: J2.2 (COM), R4.2
unnamed: N4.4 (TXD), R7.1, U7.13
unnamed: N4.5 (RXD), R5.1, R6.2
unnamed: N4.6 (~RTS), R9.1, U7.9, U7.10
unnamed: R10.1, U7.12, U9.4 (RXD)
unnamed: U7.3, U7.4, U7.5

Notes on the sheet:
Filter Capacitors
Reset Circuitry
Programmer
UART Circuitry
5V Power Supply
Unused
Note: U7 has VCC connected to pin 14 and GND connected to pin 7.
Encoder Amplifiers
Sonar Connectors
Motor Circuitry
In Circuit Programmer Circuitry
Bus Circuitry
Mounting Holes
Open Source Hardware Logo
Microcontroller + Crystal
35V Aluminum
6.3V Tantalum

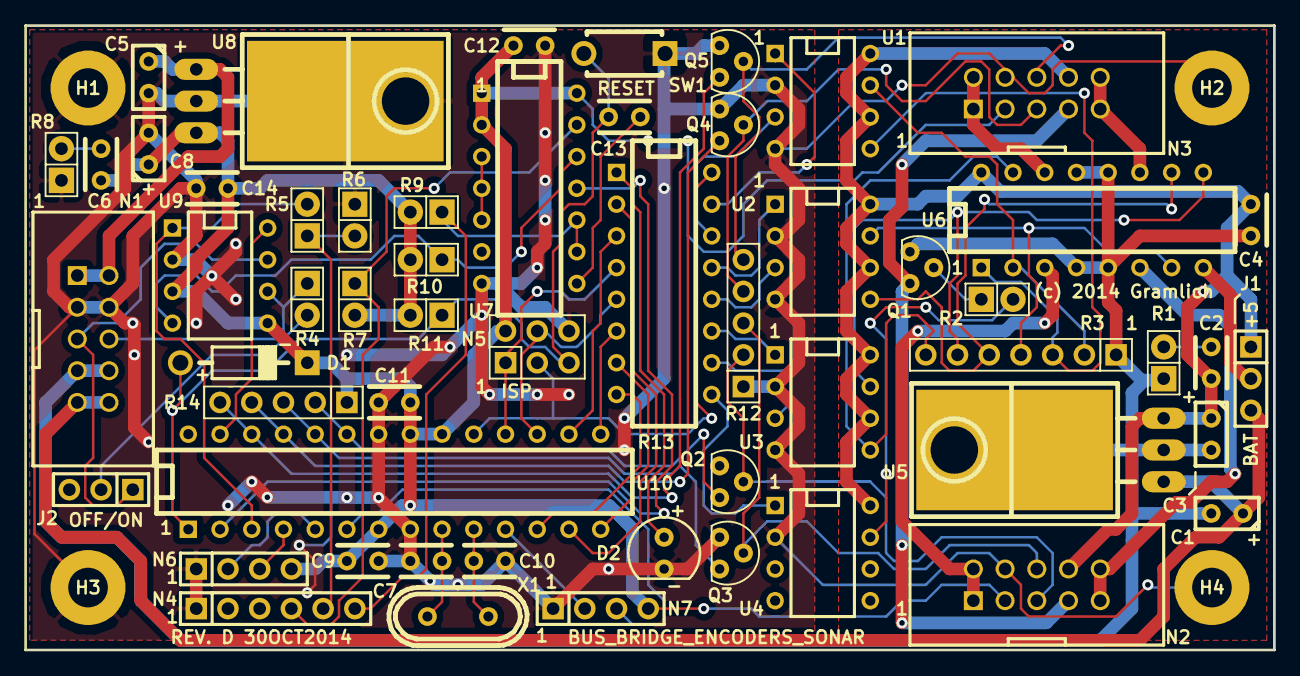
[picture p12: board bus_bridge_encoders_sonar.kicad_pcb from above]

Board: 2 copper layers, 100.0 x 50.0 mm, 61 parts (1 on the bottom side), 65 nets.

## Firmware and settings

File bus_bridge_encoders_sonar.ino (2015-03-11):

// Copyright (c) 2014-2015 by Wayne C. Gramlich.  All rights reserved.
// Some code came from the ros_arduino_bridge.

// The following tests are implemented by this code:
#define TEST_BUS_INPUT 1
#define TEST_BUS_OUTPUT 2
#define TEST_BUS_ECHO 3
#define TEST_BUS_COMMAND 4

// Set TEST to one of the possible tests:
#define TEST TEST_BUS_COMMAND

// Watch-out the code for SerialHardwared.cpp has been modified to
// notice this #define.  It causes the 8-ibt interrupt driver for
// UART1 to be disabled:
#define UART1_DISABLED

#include <Bus_Slave.h>
#include "Bus_Bridge_Encoders_Sonar_Local.h"

// The null object can be used for *debug_uart*:
NULL_UART null_uart;

// Debug *debug_uart* and *bus_uart* pointers:
#if defined(UDR1)
  UART *debug_uart = (UART *)&avr_uart0;
  UART *bus_uart = (UART *)&avr_uart1;
#else // defined(UDR1)
  UART *debug_uart = (UART *)&null_uart;
  UART *bus_uart = (UART *)&avr_uart0;
#endif // defined(UDR1)

// Define the pin names alphabetically:
static const UByte bus_standby_pin = A4;
static const UByte direction_1a_pin = 7;
static const UByte direction_enable_12_pin = 10;
static const UByte direction_2a_pin = 12;
static const UByte direction_3a_pin = 11;
static const UByte direction_enable_34_pin = 9;
static const UByte direction_enable_4a_pin = 8;
static const UByte encoder1_phase_a_pin = A0;
static const UByte encoder1_phase_b_pin = A1;
static const UByte encoder2_phase_a_pin = A2;
static const UByte encoder2_phase_b_pin = A3;
static const UByte encoders_enable_pin = 6;
static const UByte led_pin = 13;

// Encoder buffer:
#define BUFFER_POWER 8
#define BUFFER_SIZE (1 << BUFFER_POWER)
#define BUFFER_MASK (BUFFER_SIZE - 1)
static UByte encoder_buffer[BUFFER_SIZE];
static volatile UByte encoder_buffer_in = 0;
static volatile UByte encoder_buffer_out = 0;

// There are two encoders:
//
//    Encoder   Phase  Arduino Pin   PCInt
//    =======   =====  ===========   =======
//      1	  A        A0        PCInt8
//      1         B        A1        PCInt9
//      2         A        A2        PCInt10
//      2         B        A3        PCInt11

// This table is computed by bus_bridge_encoders_sonar.py
// Please read the comment in the Python code to understand
// the structure of the *state_transition_table* below:
static Byte state_transition_table[32] = {
    //            ccccc         sgg   // [xx]: SGG[gg] => sgg +/-
    (signed char)((0x00 << 3) | 0x0), // [00]: 000[00] => 000  0
    (signed char)((0x1f << 3) | 0x4), // [01]: 001[00] => 100 -1
    (signed char)((0x01 << 3) | 0x0), // [02]: 010[00] => 000 +1
    (signed char)((0x02 << 3) | 0x0), // [03]: 011[00] => 000 +2
    (signed char)((0x00 << 3) | 0x4), // [04]: 100[00] => 100  0
    (signed char)((0x1f << 3) | 0x4), // [05]: 101[00] => 100 -1
    (signed char)((0x01 << 3) | 0x0), // [06]: 110[00] => 000 +1
    (signed char)((0x1e << 3) | 0x4), // [07]: 111[00] => 100 -2
    (signed char)((0x01 << 3) | 0x1), // [08]: 1000[01] => 001 +1
    (signed char)((0x00 << 3) | 0x1), // [09]: 1001[01] => 001  0
    (signed char)((0x02 << 3) | 0x1), // [10]: 1010[01] => 001 +2
    (signed char)((0x1f << 3) | 0x5), // [11]: 1011[01] => 101 -1
    (signed char)((0x01 << 3) | 0x1), // [12]: 1100[01] => 001 +1
    (signed char)((0x00 << 3) | 0x5), // [13]: 1101[01] => 101  0
    (signed char)((0x1e << 3) | 0x5), // [14]: 1110[01] => 101 -2
    (signed char)((0x1f << 3) | 0x5), // [15]: 1111[01] => 101 -1
    (signed char)((0x1f << 3) | 0x6), // [16]: 10000[10] => 110 -1
    (signed char)((0x02 << 3) | 0x2), // [17]: 10001[10] => 010 +2
    (signed char)((0x00 << 3) | 0x2), // [18]: 10010[10] => 010  0
    (signed char)((0x01 << 3) | 0x2), // [19]: 10011[10] => 010 +1
    (signed char)((0x1f << 3) | 0x6), // [20]: 10100[10] => 110 -1
    (signed char)((0x1e << 3) | 0x6), // [21]: 10101[10] => 110 -2
    (signed char)((0x00 << 3) | 0x6), // [22]: 10110[10] => 110  0
    (signed char)((0x01 << 3) | 0x2), // [23]: 10111[10] => 010 +1
    (signed char)((0x02 << 3) | 0x3), // [24]: 11000[11] => 011 +2
    (signed char)((0x01 << 3) | 0x3), // [25]: 11001[11] => 011 +1
    (signed char)((0x1f << 3) | 0x7), // [26]: 11010[11] => 111 -1
    (signed char)((0x00 << 3) | 0x3), // [27]: 11011[11] => 011  0
    (signed char)((0x1e << 3) | 0x7), // [28]: 11100[11] => 111 -2
    (signed char)((0x01 << 3) | 0x3), // [29]: 11101[11] => 011 +1
    (signed char)((0x1f << 3) | 0x7), // [30]: 11110[11] => 111 -1
    (signed char)((0x00 << 3) | 0x7), // [31]: 11111[11] => 111  0
};

// PID constants:

// *PCINT1_vect*() is the interrupt service routine for the
// pin change interrupts PCINT8/.../15.  The two encoders are
// attached to PCINT8/9/10/11, so these are the bits we want
// to capture.  This routine just stuffs the encoder bits
// into a buffer:

ISR(PCINT1_vect) {
  // Stuff the port C input bits into *buffer* and advance *buffer_in*:
  encoder_buffer[encoder_buffer_in] = PINC;
  encoder_buffer_in = (encoder_buffer_in + 1) & BUFFER_MASK;
  //Serial.print('.');
  //UDR0 = '.';
}

Bus_Slave bus_slave(bus_uart, debug_uart);
Bus_Bridge_Encoders_Sonar bus_bridge_encoders_sonar(33);

UByte command_process(Bus_Slave *bus_slave, 
 UByte command, Logical execute_mode) {
  return bus_bridge_encoders_sonar.command_process(bus_slave,
   command, execute_mode);
}

void loop() {
  switch (TEST) {
    case TEST_BUS_COMMAND: {
      // Encoder positions and state:
      static UByte encoder1_state = 0;
      static UByte encoder2_state = 0;

      // Deal with any *bus* related activities:
      bus_slave.slave_mode(0x21, command_process);

      // Deal with encoder issues:
      if (encoder_buffer_in != encoder_buffer_out) {
	// Grab all 4 encoder bits from *encoder_buffer*:
	UByte encoder_bits = encoder_buffer[encoder_buffer_out];
	encoder_buffer_out = (encoder_buffer_out + 1) & BUFFER_MASK;

	// Just print out *encoder_bits*:
	//Serial.print(encoder_bits & 0x3);
	//Serial.print(":");
	//Serial.print((encoder_bits >> 2) & 0x3);
	//Serial.print("\n");

	// Process encoder1:
	// *encoder1_state* has 3 bits of state - '0000 0sss'.
	// We take encoder1 bits encoder from *encoder_bits* ('0000 00ee'),
	// shift them left by 3, and OR them with the *encoder1_state*:
	//
	//     encoder1_state:  0000 0sss
	//     encoder_bits<<3: 000e e000
	//  OR ==========================
	//     index            000e esss
	//
	UByte index = ((encoder_bits & 0x3) << 3) | encoder1_state;

	// Note that *state_transition* is signed.
	Byte state_transition = state_transition_table[index];
	bus_bridge_encoders_sonar._encoder1 += state_transition >> 3;
	encoder1_state = (unsigned char)(state_transition & 0x7);

	// Process encoder2:
	// Now we do the same for encoder2 whose bits are 2 bits over
	// ('0000 eexx'):
	index = ((encoder_bits & 0xc) << 1) | encoder2_state;
	state_transition = state_transition_table[index];
	bus_bridge_encoders_sonar._encoder2 += state_transition >> 3;
	encoder2_state = (unsigned char)(state_transition & 0x7);
      }
      break;
    }
    case TEST_BUS_ECHO: {
      // Wait for a *frame* to show up on *bus*:
      UShort frame = bus_slave.frame_get();

      // Set the *LED* to the least significant bit of *frame*:
      if ((frame & 1) == 0) {
        digitalWrite(led_pin, LOW);
      } else {
        digitalWrite(led_pin, HIGH);
      }

      // Print *frame* out to *debug_uart*:
      debug_uart->frame_put(frame & 0x7f);

      // Send out a CRLF when we get a '_':
      if (frame == (UShort)'_') {
        debug_uart->string_print((Character *)"\r\n");
      }

      // Now send *frame* back to the *bus*:
      bus_slave.frame_put(frame);

      // Get the *echo_frame* and check for a mismatch;
      UShort echo_frame = bus_slave.frame_get();
      if (frame != echo_frame) {
        debug_uart->string_print((Character *)"!");
      }

      break;
    }
    case TEST_BUS_OUTPUT: {
      // This test will just output characters to the debugging port
      // with no interraction with the bus:

      // Start with with *character* being static:
      static Character character = '@';

      // Just in case, make sure *character* is between '@' and '_':
      if (character < '@' || character > '_') {
	character = '@';
      }

      // Output *character* to the *debug_uart*:
      //debug_uart->frame_put((UShort)character);
      UDR0 = character;

      // Output any needed CRLF, and increment *character*:
      if (character == '_') {
	debug_uart->string_print((Character *)"\r\n");
	character = '@';
      } else {
	character += 1;
      }

      if ((character & 1) == 0) {
	digitalWrite(led_pin, LOW);
      } else {
	digitalWrite(led_pin, HIGH);
      }

      // Slow things down a little:
      delay(100);

      break;
    }
    case TEST_BUS_INPUT: {
      // This test will input *frame*'s from the *bus* and echo them
      // to *debug_uart*:

      // Get a *frame* from the bus:
      UShort frame = bus_slave.frame_get();

      // Print it out for debugging:
      debug_uart->frame_put(frame & 0x7f);

      // Tack on a CRLF when we get an '_':    
      if (frame == (UShort)'_') {
	debug_uart->string_print((Character *)"\r\n");
      }

      // Light the *LED* using the least significant bit of *frame*:
      if ((frame & 1) == 0) {
	digitalWrite(led_pin, LOW);
      } else {
	digitalWrite(led_pin, HIGH);
      }
      break;
    }
  }
}

void setup() {
  // The standard frequency for an AVR Arduino is 16MHz:
  static const UInteger frequency = (UInteger)16000000L;

  // Initalize the *debug_uart*:
  debug_uart->begin(frequency, 115200L, (Character *)"8N1");

  // Turn *LED* on:
  pinMode(led_pin, OUTPUT);
  digitalWrite(led_pin, HIGH);

  // Get *bus_uart* talking to the bus:
  bus_uart->begin(frequency, 500000L, (Character *)"9N1");

  // Force the standby pin on the CAN transeciever to low to force it
  // into active mode:
  pinMode(bus_standby_pin, OUTPUT);
  digitalWrite(bus_standby_pin, LOW);

  // Set up the H-Bridge pins:
  pinMode(direction_1a_pin, OUTPUT);
  pinMode(direction_enable_12_pin, OUTPUT);
  pinMode(direction_2a_pin, OUTPUT);
  pinMode(direction_3a_pin, OUTPUT);
  pinMode(direction_enable_34_pin, OUTPUT);
  pinMode(direction_enable_4a_pin, OUTPUT);  

  // Disable the motors:
  digitalWrite(direction_1a_pin, LOW);
  digitalWrite(direction_enable_12_pin, LOW);
  digitalWrite(direction_2a_pin, LOW);
  digitalWrite(direction_3a_pin, LOW);
  digitalWrite(direction_enable_34_pin, LOW);
  digitalWrite(direction_enable_4a_pin, LOW);

  // Set up the encoder pins:
  pinMode(encoder1_phase_a_pin, INPUT);
  pinMode(encoder1_phase_b_pin, INPUT);
  pinMode(encoder2_phase_a_pin, INPUT);
  pinMode(encoder2_phase_b_pin, INPUT);
  pinMode(encoders_enable_pin, OUTPUT);

  // Turn on encoder LED's:
  digitalWrite(encoders_enable_pin, HIGH);

  // Set up Interrupt on Pin Change interrupt vector.  The encoder
  // pins are attached to PCINT8/9/10/11, so we only need to set
  // PCMSK1 to '0000 1111':
  PCMSK1 = _BV(3) | _BV(2) | _BV(1) | _BV(0);

  // Now enable interrup on changes for PCINT8/.../15, by setting
  // PCICR to 1.  Thus, PCICR is set to 'xxxx x010' or '0000 0010':
  PCICR = _BV(1);

  // Enable global interrupts by setting the I bit (7th bit) in the
  // status register:
  //SREG |= _BV(7);

  // Enable/disable interrupts based on *TEST*:
  switch (TEST) {
    case TEST_BUS_OUTPUT:
      debug_uart = &avr_uart0;
      debug_uart->begin(frequency, 115200L, (Text)"8N1");
      debug_uart->string_print((Character *)"\r\nbbes_output:\r\n");
      debug_uart->interrupt_set((Logical)0);
      bus_uart->interrupt_set((Logical)0);
      break;
    case TEST_BUS_INPUT:
      debug_uart->string_print((Character *)"\r\nbbes_input:\r\n");
      debug_uart->interrupt_set((Logical)1);
      bus_uart->interrupt_set((Logical)1);
      break;
    case TEST_BUS_ECHO:
      debug_uart->string_print((Character *)"\r\nbbes_echo:\r\n");
      debug_uart->interrupt_set((Logical)0);
      bus_uart->interrupt_set((Logical)0);
      break;
    case TEST_BUS_COMMAND:
      debug_uart->string_print((Character *)"\r\nbbes_command:\r\n");
      debug_uart->interrupt_set((Logical)1);
      bus_uart->interrupt_set((Logical)1);
      break;
  }
}

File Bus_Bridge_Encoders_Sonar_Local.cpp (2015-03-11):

// Generated file: only edit in designated areas!
#include <Bus_Bridge_Encoders_Sonar_Local.h>
#include <Bus_Slave.h>

// Put top level includes, typedef's here:
  //////// Edit begins here: TOP_LEVEL
  //////// Edit ends here: TOP_LEVEL

// Constructor
Bus_Bridge_Encoders_Sonar::Bus_Bridge_Encoders_Sonar(UByte address) {
  //////// Edit begins here: CONSTRUCTOR
  led_set(1);
  encoder1_set(0);
  encoder2_set(0);
  encoder1_reverse_set((Logical)0);
  encoder2_reverse_set((Logical)0);
  motor1_set(0);
  motor2_set(0);
  motor1_reverse_set((Logical)1);
  motor2_reverse_set((Logical)1);
  motors_encoders_swap_set((Logical)1);
  pid_active_set((Logical)0);
  pid_denominator_set(50);
  pid_derivative_set(12);
  pid_integral_set(0);
  pid_proportional_set(20);
  //////// Edit ends here: CONSTRUCTOR
}

// led_get: LED to control
Logical Bus_Bridge_Encoders_Sonar::led_get() {
  Logical result = 0;
  //////// Edit begins here: LED_GET
  result = _led;
  //////// Edit ends here: LED_GET
  return result;
}

// led_set: LED to control
void Bus_Bridge_Encoders_Sonar::led_set(Logical led) {
  //////// Edit begins here: LED_SET
  _led = led;
  digitalWrite(13, led);
  //////// Edit ends here: LED_SET
}

// encoder1_get: Encoder 1
Integer Bus_Bridge_Encoders_Sonar::encoder1_get() {
  Integer result = 0;
  //////// Edit begins here: ENCODER1_GET
  Integer encoder = _motors_encoders_swap ? _encoder2 :_encoder1;
  if (_encoder1_reverse) {
    encoder = -encoder;
  }
  result = encoder;
  //////// Edit ends here: ENCODER1_GET
  return result;
}

// encoder1_set: Encoder 1
void Bus_Bridge_Encoders_Sonar::encoder1_set(Integer encoder1) {
  //////// Edit begins here: ENCODER1_SET
  if (_encoder1_reverse) {
    encoder1 = -encoder1;
  }
  if (_motors_encoders_swap) {
    _encoder2 = encoder1;
  } else {
    _encoder1 = encoder1;
  }
  //////// Edit ends here: ENCODER1_SET
}

// encoder2_get: Encoder 2
Integer Bus_Bridge_Encoders_Sonar::encoder2_get() {
  Integer result = 0;
  //////// Edit begins here: ENCODER2_GET
  Integer encoder = _motors_encoders_swap ? _encoder1 :_encoder2;
  if (_encoder2_reverse) {
    encoder = -encoder;
  }
  result = encoder;
  //////// Edit ends here: ENCODER2_GET
  return result;
}

// encoder2_set: Encoder 2
void Bus_Bridge_Encoders_Sonar::encoder2_set(Integer encoder2) {
  //////// Edit begins here: ENCODER2_SET
  if (_encoder2_reverse) {
    encoder2 = -encoder2;
  }
  if (_motors_encoders_swap) {
    _encoder1 = encoder2;
  } else {
    _encoder2 = encoder2;
  }
  //////// Edit ends here: ENCODER2_SET
}

// motor1_get: Motor 1
Byte Bus_Bridge_Encoders_Sonar::motor1_get() {
  Byte result = 0;
  //////// Edit begins here: MOTOR1_GET
  result = _motor1;
  //////// Edit ends here: MOTOR1_GET
  return result;
}

// motor1_set: Motor 1
void Bus_Bridge_Encoders_Sonar::motor1_set(Byte motor1) {
  //////// Edit begins here: MOTOR1_SET

  // Save *motor1* for future reads:
  _motor1 = motor1;

  // Set the direction pins:
  Logical pin1 = (Logical)0;
  Logical pin2 = (Logical)1;
  if ((motor1 > 0 && _motor1_reverse) || (motor1 < 0 && !_motor1_reverse)) {
    // Reverse the motor direction:
    pin1 = (Logical)1;
    pin2 = (Logical)0;
  } else if ((motor1 & 0x7f) == 0) {
    // Put the motor into "brake" mode:
    pin2 = (Logical)0;
  } // else leave the motor in the forward direction:

  // Compute *pwm* (Pulse Width Modulation) value from *motor1*:
  if (motor1 < 0) {
    motor1 = -motor1;
  }
  UByte pwm = ((UByte)motor1 & 0x7f) << 1;
  if (motor1 == 0x80) {
    // A speed of 0x80 (== (Byte)-128), is full brake mode:
    pwm = 0xff;
  }
  if (_motors_encoders_swap) {
    digitalWrite(_direction_3a_pin, pin1);
    digitalWrite(_direction_4a_pin, pin2);
    analogWrite(_direction_enable_34_pin, pwm);
  } else {
    digitalWrite(_direction_1a_pin, pin1);
    digitalWrite(_direction_2a_pin, pin2);
    analogWrite(_direction_enable_12_pin, pwm);
  }
  //////// Edit ends here: MOTOR1_SET
}

// motor2_get: Motor 2
Byte Bus_Bridge_Encoders_Sonar::motor2_get() {
  Byte result = 0;
  //////// Edit begins here: MOTOR2_GET
  result = _motor2;
  //////// Edit ends here: MOTOR2_GET
  return result;
}

// motor2_set: Motor 2
void Bus_Bridge_Encoders_Sonar::motor2_set(Byte motor2) {
  //////// Edit begins here: MOTOR2_SET

  // Save *motor2* for future reads:
  _motor2 = motor2;

  // Set the direction pins:
  Logical pin1 = (Logical)0;
  Logical pin2 = (Logical)1;
  if ((motor2 > 0 && _motor2_reverse) || (motor2 < 0 && !_motor2_reverse)) {
    // Reverse the motor direction:
    pin1 = (Logical)1;
    pin2 = (Logical)0;
  } else if ((motor2 & 0x7f) == 0) {
    // Put the motor into "brake" mode:
    pin2 = (Logical)0;
  } // else leave the motor in the forward direction:

  // Compute *pwm* (Pulse Width Modulation) value from *motor2*:
  if (motor2 < 0) {
    motor2 = -motor2;
  }
  UByte pwm = ((UByte)motor2 & 0x7f) << 1;
  if (motor2 == 0x80) {
    // A speed of 0x80 (== (Byte)-128), is full brake mode:
    pwm = 0xff;
  }
  if (_motors_encoders_swap) {
    analogWrite(_direction_enable_12_pin, pwm);
    digitalWrite(_direction_1a_pin, pin1);
    digitalWrite(_direction_2a_pin, pin2);
  } else {
    analogWrite(_direction_enable_34_pin, pwm);
    digitalWrite(_direction_3a_pin, pin1);
    digitalWrite(_direction_4a_pin, pin2);
  }
  //////// Edit ends here: MOTOR2_SET
}

// motor1_reverse_get: Toggle motor1 direction.
Logical Bus_Bridge_Encoders_Sonar::motor1_reverse_get() {
  Logical result = 0;
  //////// Edit begins here: MOTOR1_REVERSE_GET
  result = _motor1_reverse;
  //////// Edit ends here: MOTOR1_REVERSE_GET
  return result;
}

// motor1_reverse_set: Toggle motor1 direction.
void Bus_Bridge_Encoders_Sonar::motor1_reverse_set(Logical motor1_reverse) {
  //////// Edit begins here: MOTOR1_REVERSE_SET
  _motor1_reverse = motor1_reverse;
  //////// Edit ends here: MOTOR1_REVERSE_SET
}

// motor2_reverse_get: Toggle motor2 direction.
Logical Bus_Bridge_Encoders_Sonar::motor2_reverse_get() {
  Logical result = 0;
  //////// Edit begins here: MOTOR2_REVERSE_GET
  result = _motor2_reverse;
  //////// Edit ends here: MOTOR2_REVERSE_GET
  return result;
}

// motor2_reverse_set: Toggle motor2 direction.
void Bus_Bridge_Encoders_Sonar::motor2_reverse_set(Logical motor2_reverse) {
  //////// Edit begins here: MOTOR2_REVERSE_SET
  _motor2_reverse = motor2_reverse;
  //////// Edit ends here: MOTOR2_REVERSE_SET
}

// encoder1_reverse_get: Toggle encoder1 direction.
Logical Bus_Bridge_Encoders_Sonar::encoder1_reverse_get() {
  Logical result = 0;
  //////// Edit begins here: ENCODER1_REVERSE_GET
  result = _encoder1_reverse;
  //////// Edit ends here: ENCODER1_REVERSE_GET
  return result;
}

// encoder1_reverse_set: Toggle encoder1 direction.
void Bus_Bridge_Encoders_Sonar::encoder1_reverse_set(Logical encoder1_reverse) {
  //////// Edit begins here: ENCODER1_REVERSE_SET
  _encoder1_reverse = encoder1_reverse;
  //////// Edit ends here: ENCODER1_REVERSE_SET
}
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

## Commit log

2014-08-12 Drew schematic for bus_bridge_encoders_sonar.
    [bus_bridge_encoders_sonar.kicad_pcb, bus_bridge_encoders_sonar.sch]
2014-08-13 Finished Rev. A board layout.
    [bus_bridge_encoders_sonar-B_Cu.gbl, bus_bridge_encoders_sonar-B_Mask.gbs, bus_bridge_encoders_sonar-B_SilkS.gbo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]
2014-08-18 Added silkscreen outline.
    [bus_bridge_encoders_sonar-B_Cu.gbl, bus_bridge_encoders_sonar-B_Mask.gbs, bus_bridge_encoders_sonar-B_SilkS.gbo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]
2014-10-02 Switched over to project local fp-lib-table.
2014-10-02 Cloned Rev. A to Rev. B.
    [bus_bridge_encoders_sonar.kicad_pcb, bus_bridge_encoders_sonar.sch]
2014-10-03 Did first cut of revision B.
    [bus_bridge_encoders_sonar-B_Cu.gbl, bus_bridge_encoders_sonar-B_Mask.gbs, bus_bridge_encoders_sonar-B_SilkS.gbo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]
2014-10-11 Rev. B is done.
    [bus_bridge_encoders_sonar-B_Cu.gbl, bus_bridge_encoders_sonar-B_Mask.gbs, bus_bridge_encoders_sonar-B_SilkS.gbo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]
2014-10-11 Cloned Rev. C from Rev. B.
    [bus_bridge_encoders_sonar.kicad_pcb, bus_bridge_encoders_sonar.sch]
2014-10-21 Forgot to commit Rev. C. Also changed vertical resistors to from pin_header to Resistor_Vertical__100 footprint.
    [bus_bridge_encoders_sonar-B_Cu.gbl, bus_bridge_encoders_sonar-B_Mask.gbs, bus_bridge_encoders_sonar-B_SilkS.gbo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]
2014-10-30 Regenerated schematics for Rev. C
2014-10-30 Cloned Rev. C into Rev. D.
    [bus_bridge_encoders_sonar.kicad_pcb, bus_bridge_encoders_sonar.sch, logic.sch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]
2014-10-30 Rev. D appears to be ready.
    [$power.sch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]
2014-11-16 Added arduino build code.
2014-12-06 Removed some ugliness from schematic.
    [$power.sch, power.sch]
2014-12-12 Got input interrupts working.
2014-12-16 Got input mode using Bus::frame_get() in poll mode.
2014-12-16 Got the interrupt test working.
2014-12-17 Did first rework of sender side refactoring.
    [bus_bridge_encoders_sonar.ino]
2014-12-21 Got primative UART0 kludged together.
2014-12-21 More UART clean-up.
2014-12-22 Redid interrupt handlers (not tested.)
2014-12-22 Got interrupts to start working.
2014-12-22 Got echo test working with interrupts.
2014-12-23 Got command test working with interrupts.
2014-12-23 Got led set/get working over bus on actual bus_bridge_encoders_sonar board.
2014-12-27 Got encoders integrated in.
2015-02-13 Split 22uF Capacitors into Aluminum and Tantalum.
    [bus_bridge_encoders_sonar.sch, logic.sch, power.sch]
2015-03-06 Switched over to Ubiquity core in Arduino.
2015-03-11 Continuing PID refactor.
2015-03-11 Converting to Motor_Encoder Class.

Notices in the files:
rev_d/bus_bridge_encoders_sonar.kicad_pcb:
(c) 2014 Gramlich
